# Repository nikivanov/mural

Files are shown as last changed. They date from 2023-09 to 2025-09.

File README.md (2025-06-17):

# [getmural.me](https://getmural.me)

Please find the main documentation on https://getmural.me. 

# Additional Information

## Positioning of the Drawing on the Wall

Here's how the image is prepared and drawn:

- The user defines the pin distance as part of the setup in the UI. For example 1 meter (or 1000mm). (This is d_pins in the image below.)
- The top margin is 20% of that distance, so the top of the image will be 200mm below the line between the two pins.
- Each side also has a 20% margin, so you'll get total of 60% of the horizontal distance, or 600mm.
- Now that we have the max width (600mm). The SVG is resized so its width is 600 and the height gets resized proportionally.
- Then a processing step is performed on the SVG to figure out what to actually draw, with each SVG unit being treated as millimeter.
- Finally it's converted into a simple format for Mural to draw, containing mostly its coordinate movement commands and pen up/down. This file is then uploaded to the microcontroller and executed line by line.

image_positioning

## Mural's Kinematic Model

Please find the kinematic model [here](KinematicModel.md).

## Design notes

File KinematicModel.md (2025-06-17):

# Mural Kinematic Model

The Mural bot is suspended on two belts. As it moves across the wall it rotates slightly,
in particular it tilts towards the center as it moves to the edges of the drawing region.

In order to achieve precise drawing abilities it is essential that Mural keeps track of its
position in space. In particular, it needs to be aware of its inclination angle as it
moves around.

## Basic Model

Here, we describe the kinematic model of Mural, which is used to derive its exact location 
and orientation in space. The model is implemented in ``movement.cpp``, in particular the function ``getBeltLengths``.

The bot is modeled as a rigid body in 2D and all features are assumed to be projected onto the wall plane.
In this representation it can be modeled as two lines: One connecting the pulley tangent points
and orthogonal to it the line which goes through the pen center and the bot's center of mass $m$. The 
two lines coincide in a reference point called $Q$. 
The distance of the two tangent points is calles $s$.
The bot's mass is assumed to be concentrated into a single point (its center of gravity) which is
located in distance $d_m$ from $Q$. The pen center is located in distance $d_p$ from $Q$ .

The relevant forces in this model are: $F_L$ applied by the left pulley, $F_R$ applied by the right pulley, 
and the gravitational force $F_G$ affecting the center of mass.

kinematic_model1

Assumptions:

- all mass is concentrated in a single point
- the belts masses are negligible
- the pin distance is much larger than the bot width $d_{pins} >> width_{bot}$ 

### Tangent points

In our model the belt connects to the bot in the tangent point of its pulley. Technically, this point 
is not fully stable: It rotates slightly around the pulley center as the bot tilts sideways.

In the following it is assumed that this rotation can be ignored, and the tangent point are fixed at
a $45^\circ$ belt angle.

tangent_point

The tangent point of the left pulley is located $q$ shifted to the right and $q$ shifted up relative to the pulley center. Likewise, the right tangent point is located $q$ left of the right pulley center and $q$ above the line connecting both pulley centers.

$q$ can be calculated from the pulley diameter $d_{pulley}$ as

$q=\frac{d_{pulley}}{2\cdot \sqrt2}$

So, for a typical pulley diameter of $d_{pulley}=12.69$ mm we get $q=4.4866$ mm .

The lenght of the line connecting the tangent point is given as the distance of the pulley axes minus $2*q$ .

## Solving for the Equilibrium State

With forces $F$ affecting the Mural bot they are moving it (translation) and rotating it by generating torques. 
We are looking for the static state of the bot, in which the forces as well as the torques cancel out.
We'll find this state by updating the values describing the bot's location, the forces and the torques 
in a consecutive and decoupled manner. I.e. while computing the forces we assume there's no torque, and while 
computing the torque there's no translating force. Updating these values repeatedly and in a loop
will lead to convergence of all quantities towards their true equilibrium states.

On a top level, we run the following steps in a loop until the quantities converge:
- compute belt angles $\varphi_L$ and $\varphi_R$
- compute forces on both belts
- compute torque on mural, solve for mural inclination $\gamma$

With the result: mural inclination $\gamma$, length of both belts in wall plane, and belt forces $F_L$ and $F_R$ .

In a subsequent step, these quantities are used to compute the belt lengths in 3D. Finally, a dilation correction is applied to account for non-rigidity of the belts under force.

## Forces

In the equilibrium state the overall torque on the bot is zero and can be ignored. In this case
all forces can be assumed to be applied to a single point:

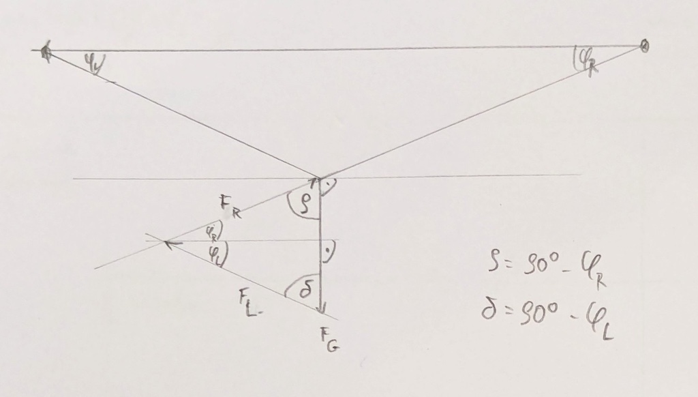
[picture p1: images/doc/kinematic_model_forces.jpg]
kinematic_model_forces


Introducing the angles $\rho = 90^\circ-\varphi_R$ and $\delta = 90^\circ-\varphi_L$ we can apply the [Law of Sines](https://en.wikipedia.org/wiki/Law_of_sines) and get:

$\frac{F_R}{F_G}=\frac{\sin(\delta)}{\sin\left( \varphi_R + \varphi_L \right)}$

$\Leftrightarrow F_R=\frac{F_G\cdot\sin(\delta)}{\sin\left( \varphi_L + \varphi_R \right)} =
\frac{F_G\cdot\cos(\varphi_L)}{\sin\left( \varphi_L + \varphi_R \right)}$

and likewise

$\frac{F_L}{F_G}=\frac{\sin(\rho)}{\sin\left( \varphi_L + \varphi_R \right)}$

$\Leftrightarrow F_L=\frac{F_G\cdot\sin(\rho)}{\sin\left( \varphi_L + \varphi_R \right)} =
\frac{F_G\cdot\cos(\varphi_R)}{\sin\left( \varphi_L + \varphi_R \right)}$

## Torques

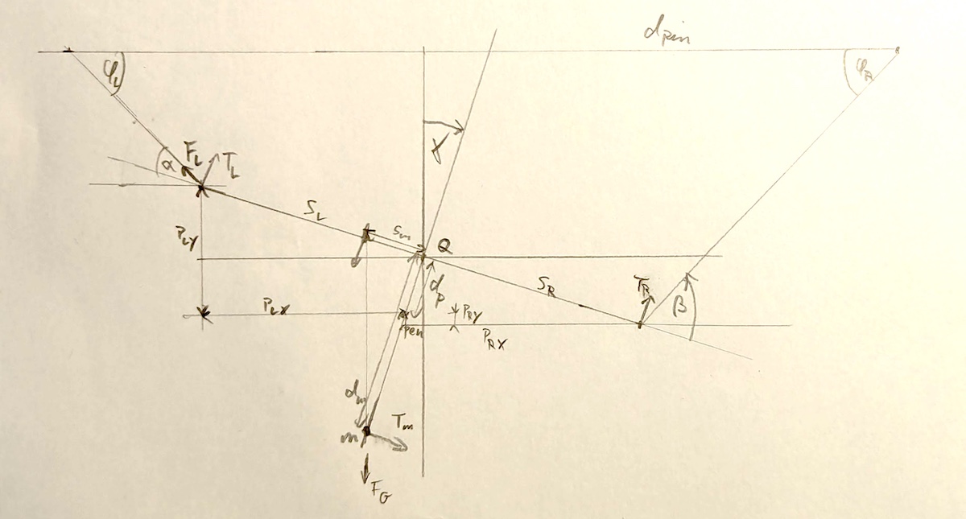
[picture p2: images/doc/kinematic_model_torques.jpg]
kinematic_model_torques


Given the forces we can compute the torque values $T_L$ ,  $T_R$ and  $T_m$ they induce around the reference point $Q$.
What we are interested in is the bot inclination angle $\gamma$. A positive $\gamma$ means the bot tilts to the right,
while a negative $\gamma$ represents a tilt to the left.

Let's introduce the auxilliary angles $\alpha$ and $\beta$ representing the direction of the belts relative to the
line connecting the tangent points:
$\varphi_L = \alpha + \gamma$
and 
$\varphi_R = \beta - \gamma$ .

As $Q$ is located in the center between the tangent points we get $s_L = 0.5\cdot s$ and $s_R = 0.5\cdot s$.

The torque induced on the left tangent point is 

$T_L = s_L \cdot \sin(\alpha)\cdot F_L$ 

, and it is pushing the bot clockwise.

Analogously, $T_R$ is affecting the right tangent point and rotating the bot counter-clockwise around $Q$:

$T_R = s_R \cdot \sin(\beta)\cdot F_R$ 

The gravity force $F_G$ of the bot results in torque $T_m$ which is rotating it counter-clockwise (for $\gamma>0$):

$T_m = s_m \cdot F_m$ , with

$s_m = d_m \cdot \tan(\gamma)$ and

$F_m = F_g \cdot \cos(\gamma)$ .

So we get

$T_m = d_m \cdot \tan(\gamma) \cdot F_G \cdot \cos(\gamma)$

In the static state the resulting torque is zero, so

$T_R - T_L + T_m \stackrel{!}{=} 0$

, and the implementation searches numerically for a $\gamma$ which fulfills this condition.

## Tangent Points given Pen Location

As our goal is to compute the precise belt lenths, we have to compute the exact tangent point location given the outcome
of the optimization operation (see ``Movement::getLeftTangentPoint``). For the left tangent point we calculate the distance from the 
pen center in $x$ and $y$ as

$P_{LX} = s_L \cdot \cos(\gamma) - d_p \cdot \sin(\gamma)$

$P_{LY} = s_L \cdot \sin(\gamma) + d_p \cdot \cos(\gamma)$

and with these the left tangent point coordinates as

$x_{PL} = x_{pen} - P_{LX}$

$y_{PL} = y_{pen} - P_{LY}$

In the same way we get for the right pulley:

$P_{RX} = s_R \cdot \cos(\gamma) + d_p \cdot \sin(\gamma)$

$P_{RY} = s_R \cdot \sin(\gamma) - d_p \cdot \cos(\gamma)$

and

$x_{PR} = x_{pen} + P_{RX}$

$y_{PR} = y_{pen} + P_{RY}$

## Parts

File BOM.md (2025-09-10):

# Bill of Materials
All parts can be found on Amazon, AliExpress, Ebay etc. Make sure the items you're ordering match the pictures. Listed prices are the lowest I could find on AliExpress.

| Part| Reference Photo | Price | Notes
|---|---|---|---|
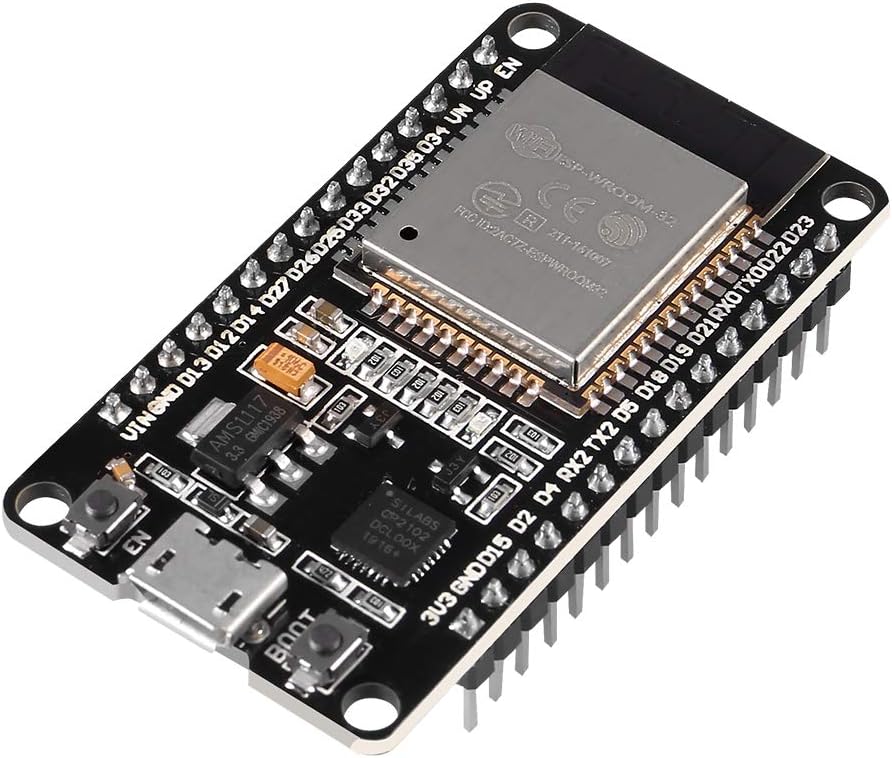
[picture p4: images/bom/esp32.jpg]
esp32
|NodeMCU ESP32 ESP-WROOM-32|| $4 | 30 pin version
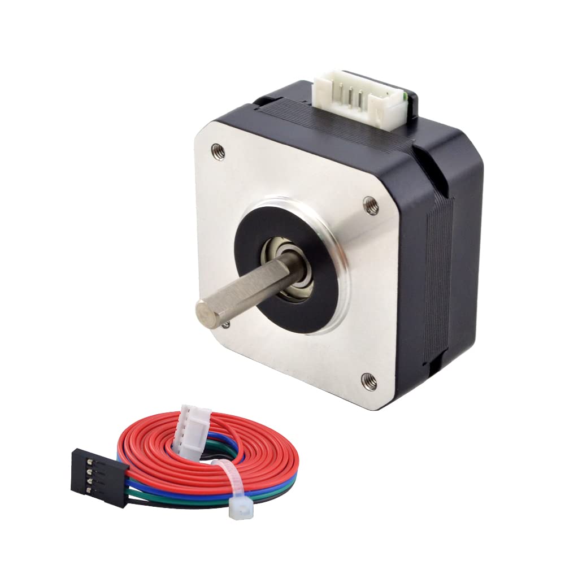
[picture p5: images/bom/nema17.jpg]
nema17
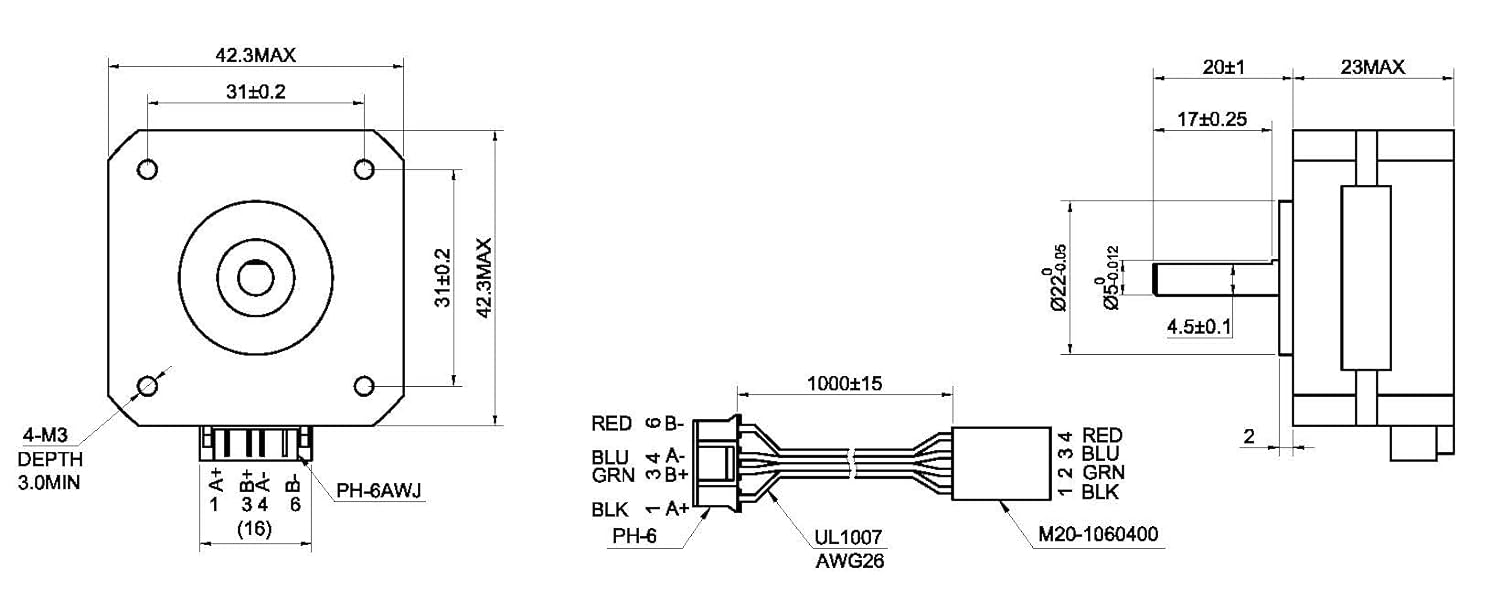
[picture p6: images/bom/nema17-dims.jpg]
nema17-dims
| 2x STEPPERONLINE Pancake Nema 17 motors |  | $18 | 
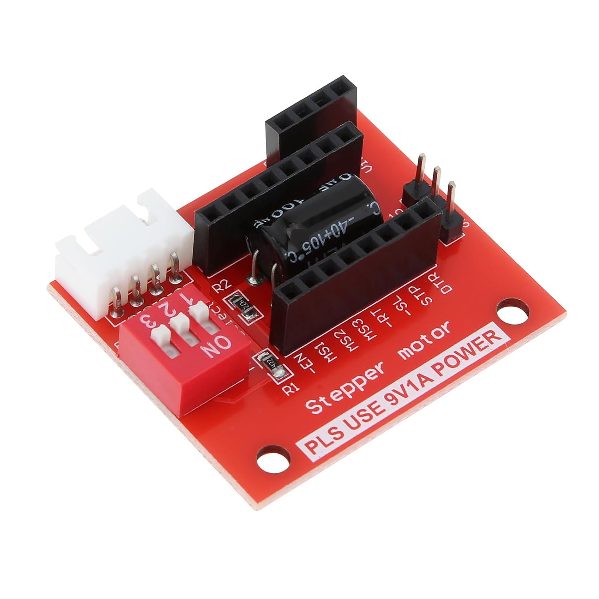
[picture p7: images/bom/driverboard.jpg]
driverboard
| 2x Stepper Motor Driver control extension boards | | $2 |
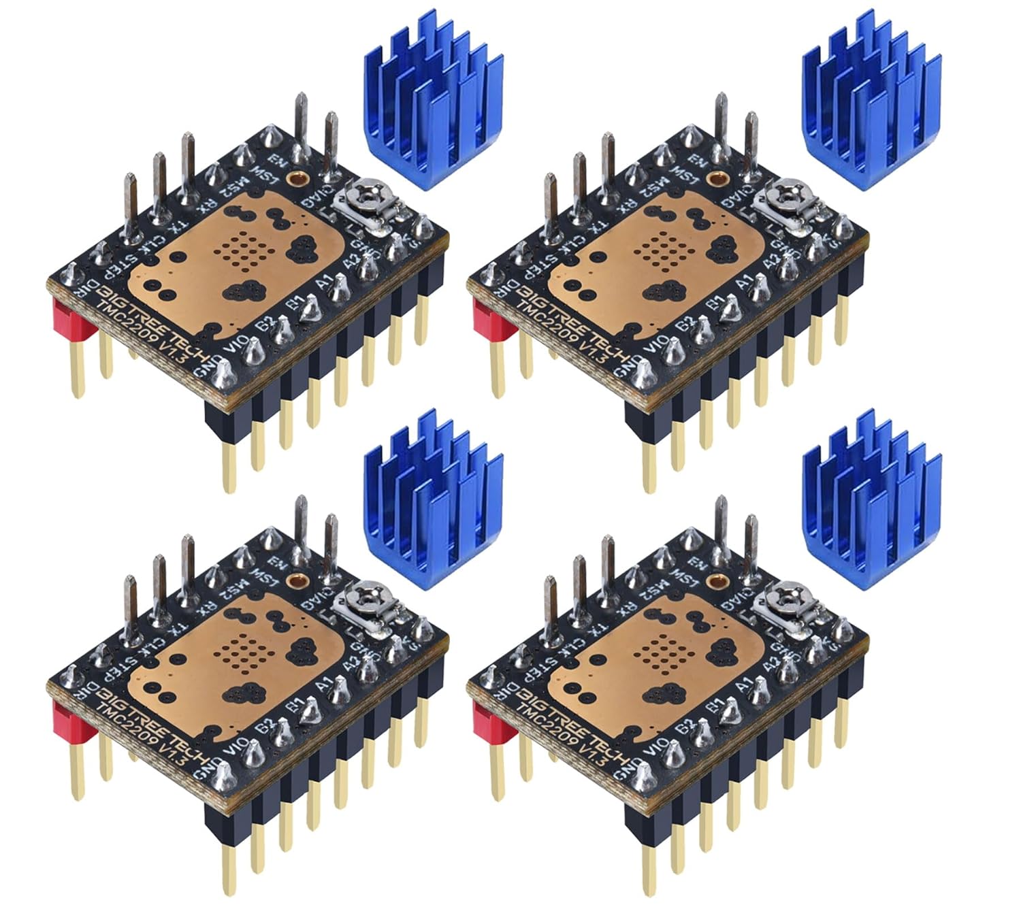
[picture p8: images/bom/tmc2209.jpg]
drivers
| 2x BigTreeTech TMC2209 Stepper motor drivers | | $14 |
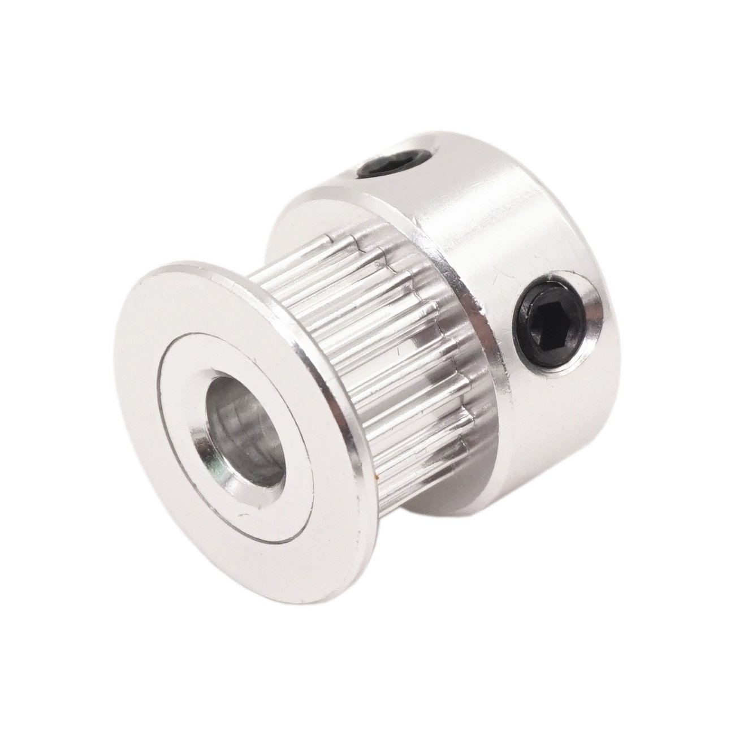
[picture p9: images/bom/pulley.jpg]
pulley
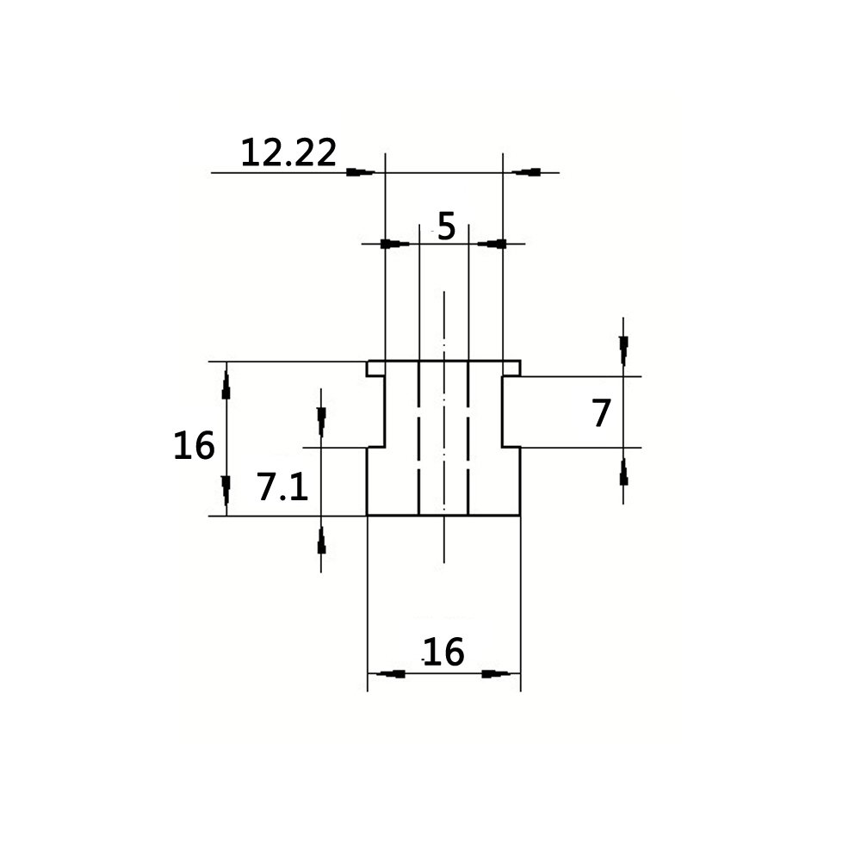
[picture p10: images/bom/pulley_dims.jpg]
pulley-dims
| 2x GT2 Pulley 20 teeth 5mm bore 6mm shaft |   | $2 | Make sure to get the pulley with those exact dimensions
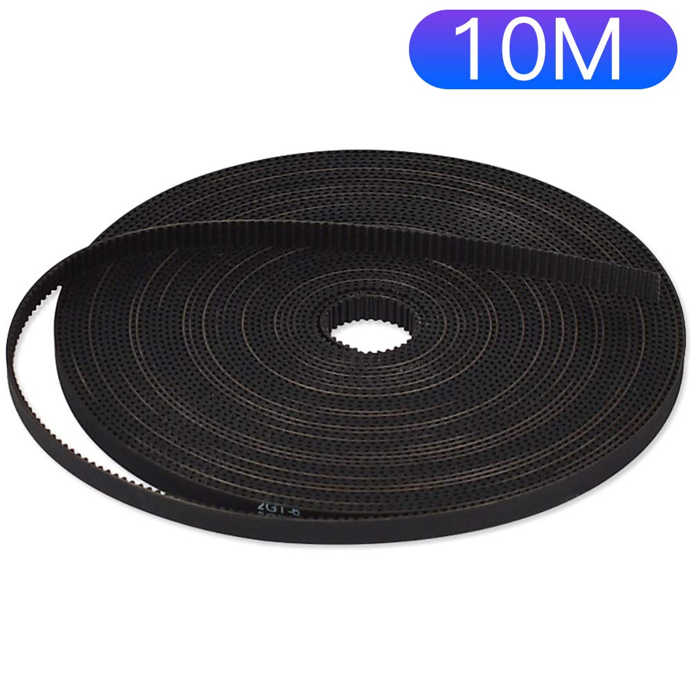
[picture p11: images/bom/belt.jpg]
belt
| GT2 Timing belt 2mm pitch 6mm width |  | $6 |
| MG90s metal gear servo | servo | $2 |
| USB-C PD trigger module | display | $1 |
| LM2596 step down voltage regulator | buck | $1 |
| 30W USB-C power delivery adapter | power | $3 | You can use any PD adapter with at least 30W and can supply 12V 
| USB-C male-to-male 10ft cable | cable | $1 |
| M-F and F-F breadboard jumper wire 10cm and 20cm | wire | $2 |
| M3 hex bolt set | m3 | $2 | You'll need 6/8/12/25 mm bolt lengths 
| 2.54m pitch male headers | headers | $1 |
| M3 heat inserts | inserts | $1 | Optional - only one is used for the pen, and you can use an M3 bolt without it
| 12mm M3 thumbscrew | thumbscrews | $1 |Optional, but sure is nicer. You only need 1 
| 10cm stepper motor cable | steppercable | $2 | These are surprisingly hard to find, I bought mine on AliExpress. You can also simply cut and solder together the long cables that came with your steppers

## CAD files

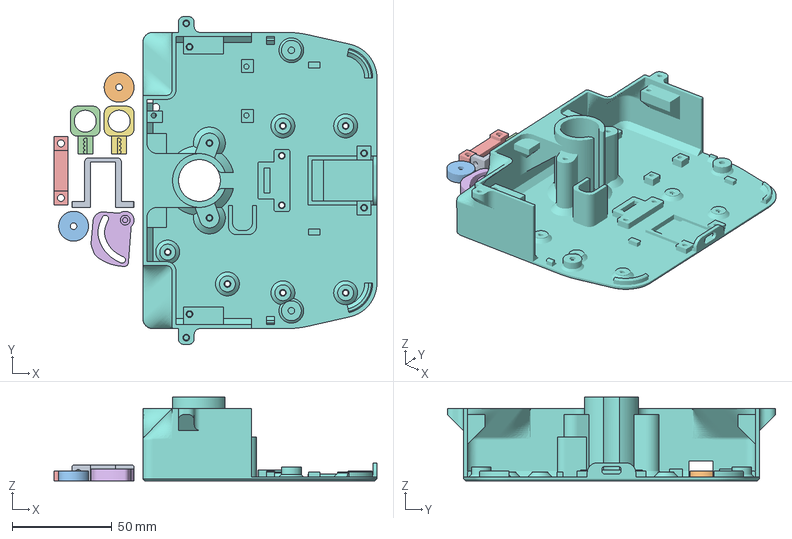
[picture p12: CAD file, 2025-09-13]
STLs/white parts.3mf
162.2 x 164.8 x 42.0 mm
white parts_1
white parts_2
white parts_3
white parts_4
white parts_5
white parts_6
white parts_7
bottom.stl

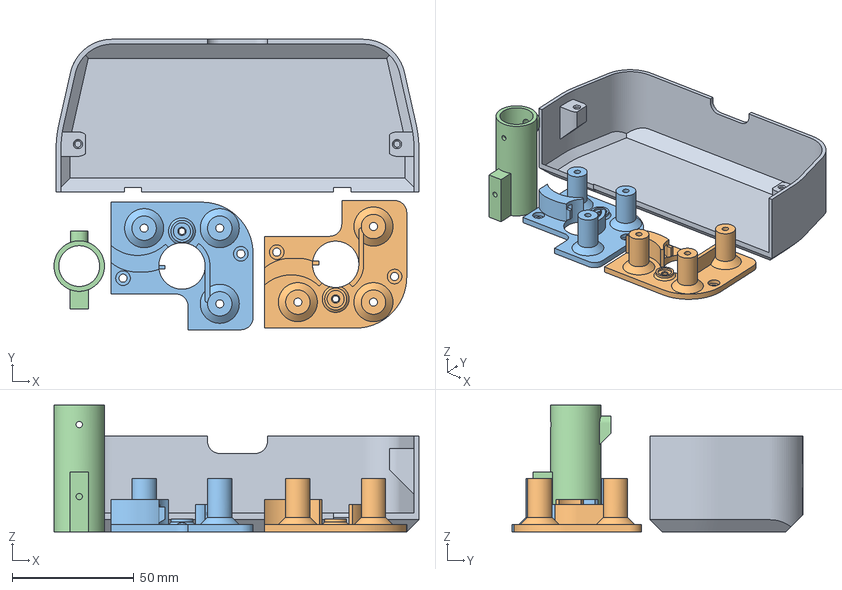
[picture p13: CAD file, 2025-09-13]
STLs/black parts.3mf
149.6 x 119.1 x 52.0 mm
black parts_1
left motor carrier.stl
right motor carrier.stl
black parts_4

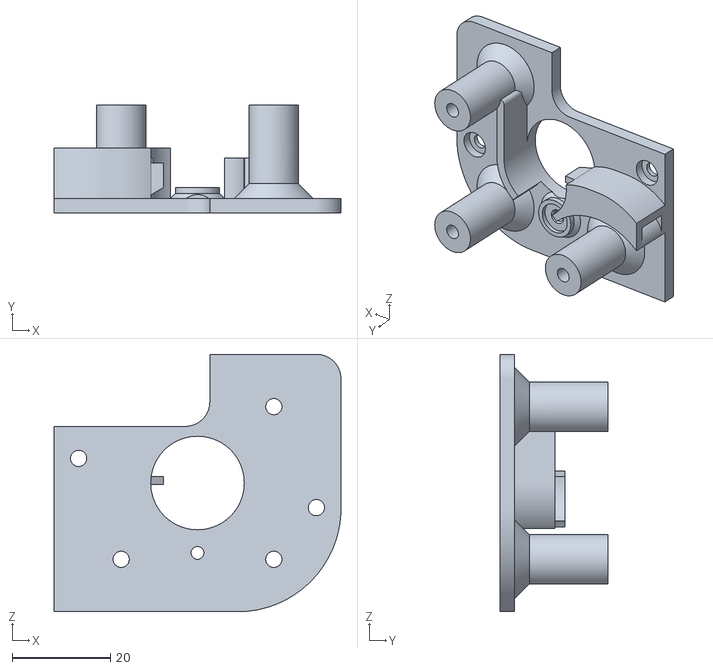
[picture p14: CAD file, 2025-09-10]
STLs/right motor carrier.stl
58.3 x 22.0 x 52.3

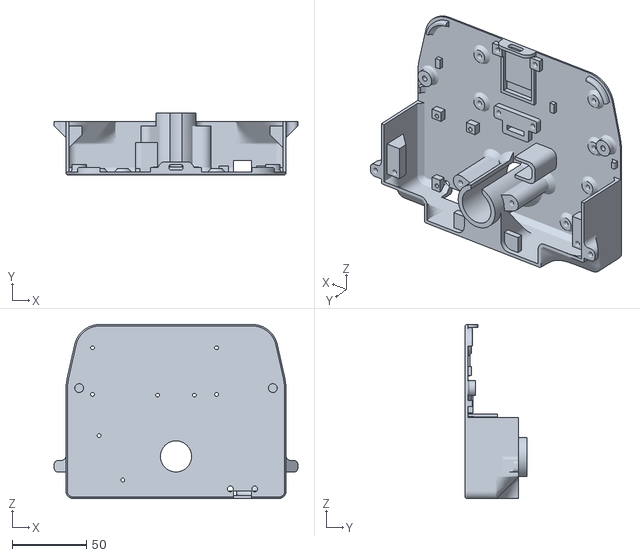
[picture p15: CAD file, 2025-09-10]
STLs/bottom.stl
164.8 x 42.0 x 117.6

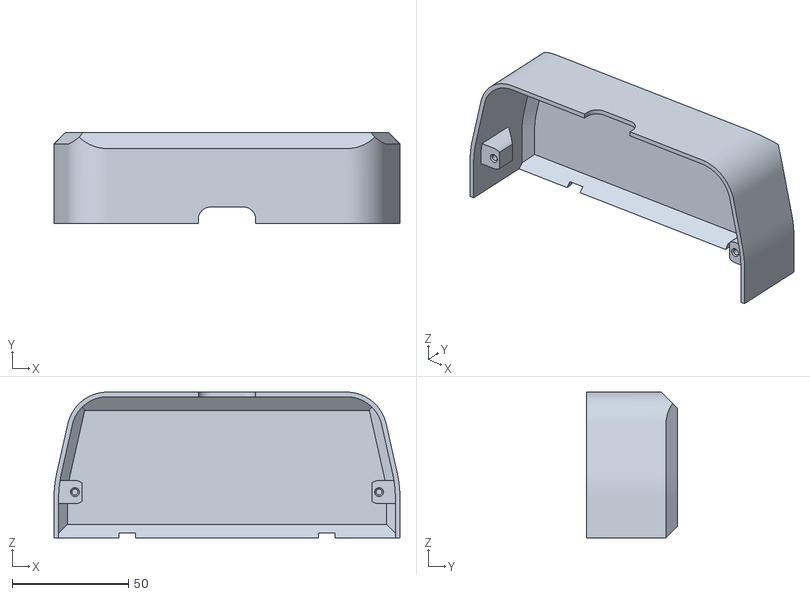
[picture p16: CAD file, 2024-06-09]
STLs/cover.stl
148.8 x 39.3 x 62.7

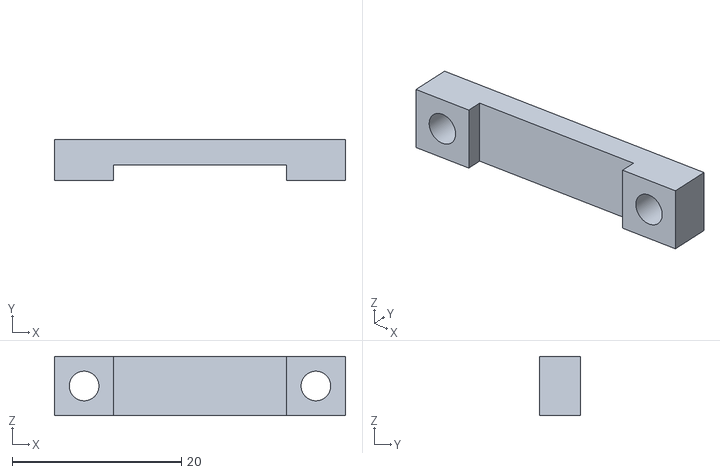
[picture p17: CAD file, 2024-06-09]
STLs/PD clamp.stl
34.4 x 4.85 x 7.00

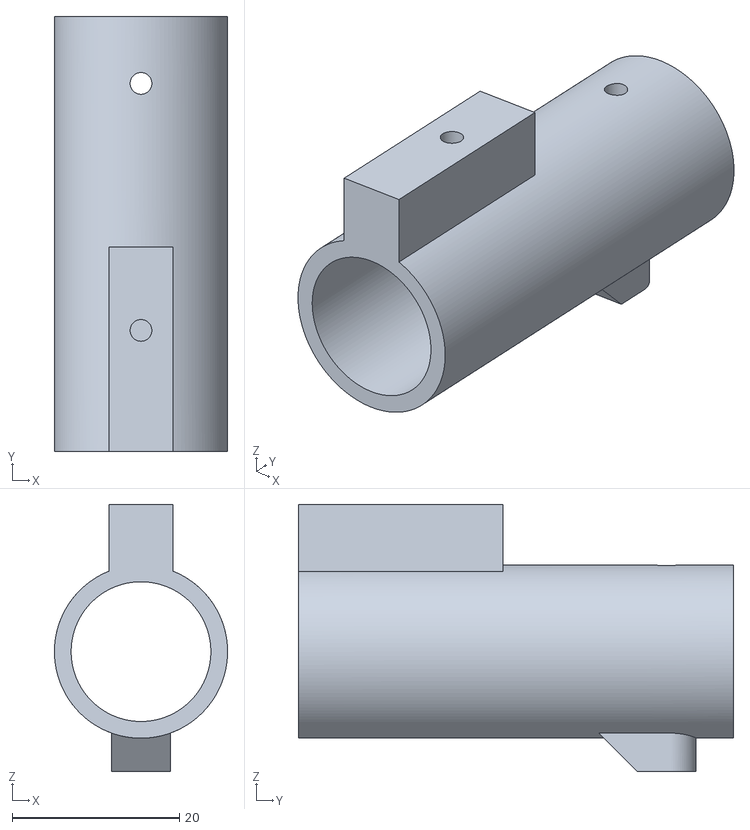
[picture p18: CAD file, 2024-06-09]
STLs/pen.stl
20.7 x 52.0 x 32.0

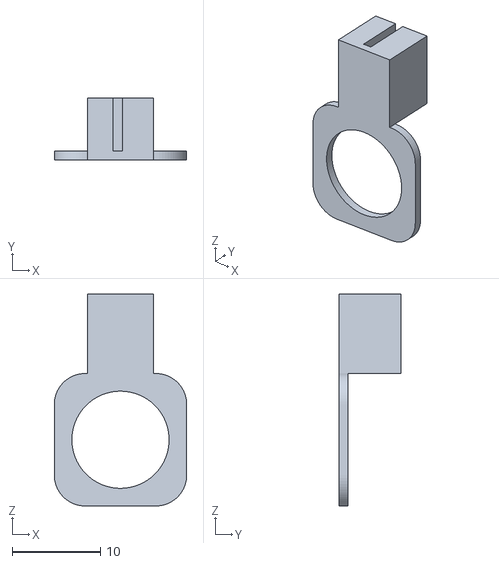
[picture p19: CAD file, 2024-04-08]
STLs/left belt loop.stl
15.0 x 7.00 x 24.0

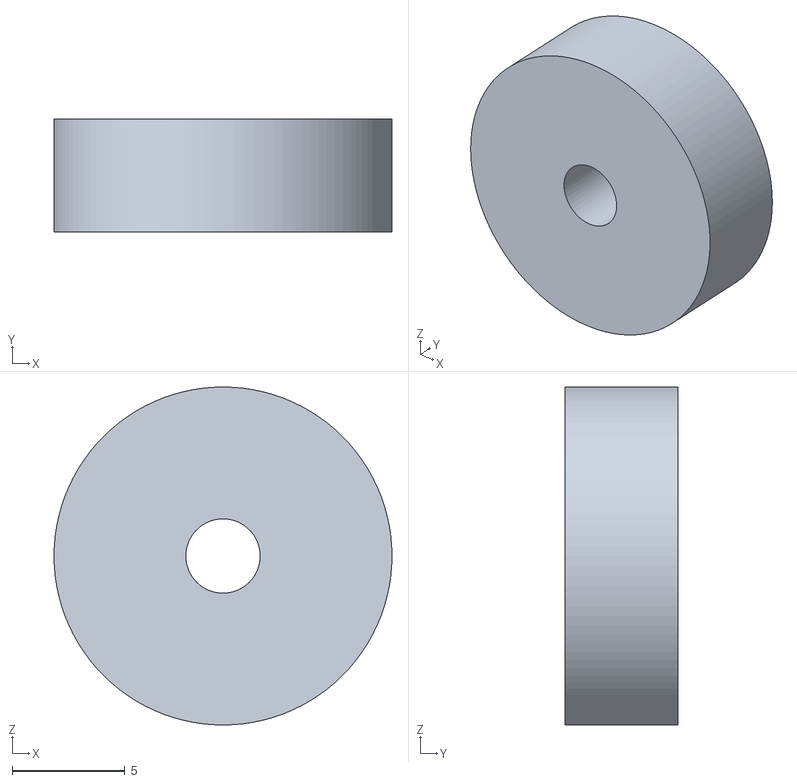
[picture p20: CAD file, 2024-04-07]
STLs/idler.stl
15.0 x 5.00 x 15.0

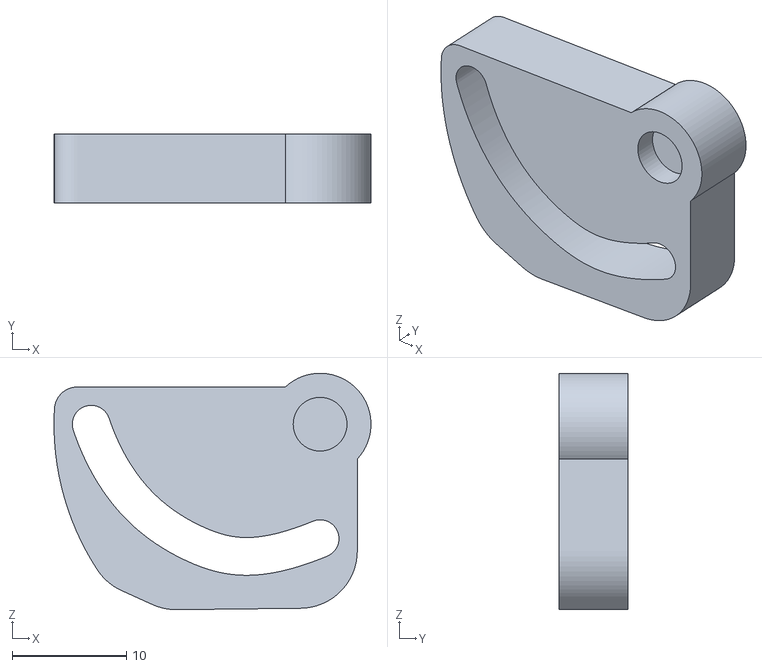
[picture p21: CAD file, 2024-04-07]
STLs/servo pen driver.stl
27.7 x 6.00 x 20.6

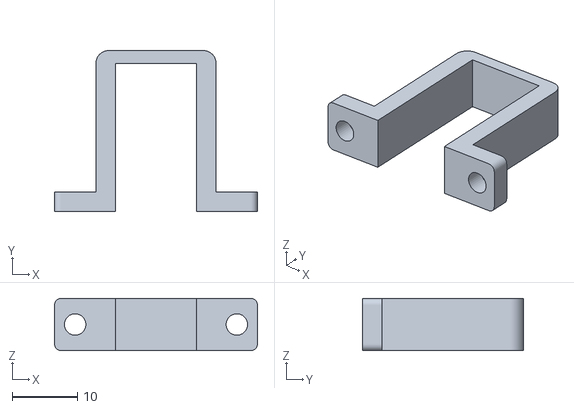
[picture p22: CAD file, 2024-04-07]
STLs/servo clamp.stl
31.2 x 24.8 x 8.00

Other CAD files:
STLs/left motor carrier.stl
STLs/right belt loop.stl

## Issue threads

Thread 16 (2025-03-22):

GCODE

rwlloyd, 2025-03-22:
Hi. Just watched your video and thought. 'Damn, this guy has done all the things I couldn't be bothered to do when I made a wall plotter a few years ago'. I approached from the modded 3D printer direction though.. RAMPS board, [Marlin-polargraph](https://github.com/i-make-robots/Marlin-polargraph) and motors suckered to a window. It was a mess of wire and a pain to set up. Your solution is much neater. Well done!

What might work is to marry the frontend and hardware that you've designed and have another board interpret gcode. The mural board would feed the gcode over serial to the GRBL board (any arduino based or the atmega328). Then 'mural-GRBL' (preconfigured for delta kinematics) handles all of the motor control.

I think that leveraging and modifying what you already have running and then having mural firmware interpret gcode would be my ideal plotter and I'd start drawing on the big windows at work asap. Your system looks very much simpler and neater than my efforts.

I guess this is not strictly an issue but I'm going to print a mural when I get the chance. Just for the hardware design I will thank you in advance.

nikivanov, 2025-03-25:
There is already an ESP32 compatible version of Grbl and a newer version, called FluidNC. I'm planning on adapting Mural to work with FluidNC so I can get all the movement goodies that it comes with.

Yash-xoxo, 2025-03-29:
thanks it might me a good upgrade

Closed 2025-04-01.

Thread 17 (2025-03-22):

CAD files

ModestoHagney, 2025-03-22:
Would you be willing to share the CAD files?

I'd like to build one of these with some parts I have on hand but I've never had much luck imorting STLs into fusion.

nikivanov, 2025-03-25:
Yep, I keep forgetting to upload F3D and STEP files. I will do it in the next few days. I'll ping this thread when it's done.

nikivanov, 2025-03-26:
https://github.com/nikivanov/mural/blob/main/STLs/Mural.step here it is!

Closed 2025-03-27.

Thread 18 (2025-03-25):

Build notes/park servo error

PangeaPrint, 2025-03-25:
First off great work! Couple things:

1. The "Park Servo" button doesn't do anything for me to control the pen holder servo. When plugged in it goes to the in/up position on boot up which works but when attaching the linear motion piece it needs to be put on in a different orientation than the video. It's really not an issue with functionality yet just wanted to add that note if anyone is seeing the same. Properly orienting it allows it to work when adjusting distance later in the prep menu.

2. Here's the wiring for the L/R servos:

4pin side               6 pin side
1-2-3-4---------------4-EMPTY-1-3-EMPTY-2
ex. Black-Green-Blue-Red------------------Red-EMPTY-Black-Blue-EMPTY-Green

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

I have the entire unit built/wired/wifi connected but one of the L/R stepper control boards showed up with the voltage adjustment screws busted so it's stuck at low voltage and won't operate under a load (ie it's own weight) without skipping until the new one comes tomorrow. That being said everything is acting correctly during bench testing.

I'm using a generic ESP32 (ESP-WROOM-32 ESP32 ESP-32S Development Board from Amazon) since I had it floating around so that may cause issue as well. I'll update tomorrow if I can get it to draw.

nikivanov, 2025-03-26:
You're absolutely right! When I was reshuffling the screens I forgot to add servo control to the Set Top Distance screen. I'll fix it now.

nikivanov, 2025-03-26:
@PangeaPrint I just uploaded the new firmware - could you try reflashing your ESP32 and let me know if that fixes your servo issue?

PangeaPrint, 2025-03-26:
Yup, that worked! One more question, not sure what the Extend 100mm (e-steps calibration) button is for but I don't see it making any movements.

nikivanov, 2025-03-26:
Yeah that one is broken too - I haven't used it in ages. I wrote it to verify the extrusion length during initial design. I'll fix it at some point.

Closed 2025-03-29.

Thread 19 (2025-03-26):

Heat inserts?

canadaohcanada, 2025-03-26:
I didn’t see the heat inserts being used in the assembly video. Is there a specific place they need to be used or is it more of a “nice to have”?

nikivanov, 2025-03-26:
7:30 into the assembly video

canadaohcanada, 2025-03-26:
Brilliant. I was watching with the sound off. Thank you for the accurate timestamp.

Closed 2025-03-26.

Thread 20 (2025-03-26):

Upload to Mural failed! [object Object] error

PangeaPrint, 2025-03-26:
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

Hitting "OK" then reloading the page is the work around.

Chrome
OSX

nikivanov, 2025-03-27:
Hmm, never seen this before. First thing we gotta do is get the actual error. I'm going to fix that e-steps calibration bug that you found and also add some code that will print the actual error instead of just the object

nikivanov, 2025-03-27:
@PangeaPrint try now please - it should be fixed. ESteps calibration should also be fixed.

Closed 2025-03-29.

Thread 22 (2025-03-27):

3d Files for byj48 Version (as seen in your Video) with unipolar to bipolar mod and MKS-DLC32

flow1986, 2025-03-27:
Hi,
very nice Project! would it be possible for you to upload the BYJ48 Stepper Version Stls?

You can use these motors with an Bipolar mod and some Bipolar Motor Drivers for more torque and less lost steps.

i want to rebuild your Mural Walldrawer with an mks-dlc32 (https://github.com/makerbase-mks/MKS-DLC32)

because it would be even cheaper and with the mks-dlc32 everything is on board (esp32, stepper driver, power supply)

i have all parts at home, because i wanted to build a wallplotter with FluidNC, but didn´t have the time yet...

thanks Flo

nikivanov, 2025-03-27:
Sure, but I wont be able to provide any support for it, and the existing firmware won't work on it. If that sounds good I can upload the STEP file

flow1986, 2025-03-27:
That Sounds perfect for me!
Thank you

Nik Ivanov ***@***.***> schrieb am Do., 27. März 2025, 15:44:

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

nikivanov, 2025-03-27:
https://github.com/nikivanov/mural/blob/28byj-48/STLs/prototype%20v8.step

Closed 2025-03-27.

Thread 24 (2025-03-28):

a problem with online firmware burning

APT-H, 2025-03-28:
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

I loved your project and planned to build one at home and play with my kids, but now the program is having a problem.

As the screenshot, I use the development board is ESP32-D0WD-V3, successfully connected to the computer, but after the motor burning, it is stuck in this step, but also waiting for a lot of time, always the same. I've replaced three computers and they all seem to have the same problem. At first, I thought that the development board was broken, but when I burned projects online in other places, I was able to burn normally and successfully run the firmware of other projects. It's weird. It's bothering me

APT-H, 2025-03-29:
I burned the source code using VSCode and it was successful.

Closed 2025-03-29.

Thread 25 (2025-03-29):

Change pins in software

ModestoHagney, 2025-03-29:
Would it be possible to add the ability to change the pins, and maybe some other settings like speed and servo positions in software?

The setpper board I'm working with uses pinouts that are different to the ones in the code.
I did manage to recompile and change the pins but I had heaps of issues getting it to compile.

nikivanov, 2025-03-29:
Hi! I'm not going to be adding support for other boards to Mural, since its hardware and software are interdependent. You're welcome to fork the repo and add these abilities if you want to make the software more generic. It sounds like you got the firmware to recompile, so you're already half way there.

ModestoHagney, 2025-03-30:
Fair enough. I had a hell of a time getting it to compile, something to do with WifiManager.git but I managed to get it on there in the end.

Closed 2025-03-30.

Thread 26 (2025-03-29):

Coordinate conversion code

CIRCUIT-RAPTOR, 2025-03-29:
Hi. I'm trying to implement a similar plotter using Raspberry pi Zeo 2W. I would like to know how the svg file uploaded is converted to coordinates for the stepper motor. Is there a specific code for doing this operation? I just want to know how the svg is converted to the final form as seen in the drawings.

nikivanov, 2025-03-29:
The code runs in your browser, with some of it running in the web worker. I rasterize and re-vectorize SVGs to account for this like stroke width.

Here's the vectorization call to the web worker: https://github.com/nikivanov/mural/blob/4682db1fa4d548cf25d1176ae29ae6e4425b6ff8/data/www/main.js#L167

Here's the call to the web worker that converts the re-vectorized SVG into a list of commands for Mural: https://github.com/nikivanov/mural/blob/4682db1fa4d548cf25d1176ae29ae6e4425b6ff8/data/www/main.js#L206

Web worker code is written in typescript and then webpacked. Here's the entry point of rendering the SVG into a list of commands: https://github.com/nikivanov/mural/blob/4682db1fa4d548cf25d1176ae29ae6e4425b6ff8/tsc/src/main.ts#L39

CIRCUIT-RAPTOR, 2025-04-03:
I was able to replicate the outline drawing function. But I'm not able to achieve the infill/crosshatch pattern in those dark areas. Any advice on how to make this work? Also, I might switch to an ESP-32 if this turns out to be unsuccessful, because I need this to be completed within 2 weeks. I'm trying to use things available at my house, that is why I went for the pi, 28byj-48 stepper motors and ULN2003 driver. If I had to use the ESP-32, would the program flashed in it via the mural website be able to run these 28byj-48 stepper motors? I saw them on your video that it was used in the first iteration.
Thanks

nikivanov, 2025-04-03:
The SVG processor will shade in any paths that have a non-white non-transparent infill. The density of the crosshatch infill is governed by this property: https://github.com/nikivanov/mural/blob/4682db1fa4d548cf25d1176ae29ae6e4425b6ff8/tsc/src/main.ts#L97

You won't be able to use the current firmware with 28byj-48 - they are driven completely differently from the steppers that I'm using.

CIRCUIT-RAPTOR, 2025-04-05:
I'm still not able to successfully create an infill code. So, I'm now using an esp-32 to flash the firmware through mural website. But I'm getting stuck at erasing flash. I've read a solved issue about the same and saw that he flashed it via VS Code in the end. Is there any fix?

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

nikivanov, 2025-04-05:
Try some of the suggestions in this thread and let me know if it helps: https://github.com/nikivanov/mural/issues/30

CIRCUIT-RAPTOR, 2025-04-05:
I've also tried those. I don't think my problem is with connecting, as from the picture it is clear that the device is connected and is able to recognize it. I tried to flash it via VS Code with Platform IO. But I'm getting errors while building:

Processing esp32dev (platform: espressif32; board: esp32dev; framework: arduino)
---------------------------------------------------------------------------------------------------------------------------------------------------------
Verbose mode can be enabled via `-v, --verbose` option
CONFIGURATION: https://docs.platformio.org/page/boards/espressif32/esp32dev.html
PLATFORM: Espressif 32 (6.10.0) > Espressif ESP32 Dev Module
HARDWARE: ESP32 240MHz, 320KB RAM, 4MB Flash
DEBUG: Current (cmsis-dap) External (cmsis-dap, esp-bridge, esp-prog, iot-bus-jtag, jlink, minimodule, olimex-arm-usb-ocd, olimex-arm-usb-ocd-h, olimex-arm-usb-tiny-h, olimex-jtag-tiny, tumpa)
PACKAGES:
 - framework-arduinoespressif32 @ 3.20017.241212+sha.dcc1105b
 - tool-esptoolpy @ 1.40501.0 (4.5.1)
 - toolchain-xtensa-esp32 @ 8.4.0+2021r2-patch5
LDF: Library Dependency Finder -> https://bit.ly/configure-pio-ldf
LDF Modes: Finder ~ chain, Compatibility ~ soft
Found 42 compatible libraries
Scanning dependencies...
Dependency Graph
|-- WiFiManager @ 2.0.17+sha.32655b7
|-- ESPAsyncWebServer @ 3.7.4+sha.25845e7
|-- ESP32Servo @ 3.0.6+sha.e697ea7
|-- Adafruit SSD1306 @ 2.5.13+sha.78d6a13
|-- AccelStepper @ 1.64.0
|-- ArduinoJson @ 5.13.4
|-- SPIFFS @ 2.0.0
|-- AsyncTCP @ 3.3.8
|-- ESPmDNS @ 2.0.0
|-- FS @ 2.0.0
|-- Wire @ 2.0.0
Building in release mode
Transpiling TS code
rm data/www/worker/* || true
'rm' is not recognized as an internal or external command,
operable program or batch file.
'true' is not recognized as an internal or external command,
operable program or batch file.
*** Error 1
npm run build
'npm' is not recognized as an internal or external command,
operable program or batch file.
*** Error 1
cp dist_packed/main.js ../data/www/worker/worker.js
'cp' is not recognized as an internal or external command,
operable program or batch file.
*** Error 1
Retrieving maximum program size .pio\build\esp32dev\firmware.elf
Checking size .pio\build\esp32dev\firmware.elf
Advanced Memory Usage is available via "PlatformIO Home > Project Inspect"
RAM:   [==        ]  15.2% (used 49796 bytes from 327680 bytes)
Flash: [========  ]  81.6% (used 1069577 bytes from 1310720 bytes)
============================================================== [SUCCESS] Took 8.94 seconds ==============================================================

I tried uploading. Even though it shows successful upload, I am not able to find the esp hotspot. I tried monitoring it and it shows a SPIFFS mounting error.

I'll provide an update if I find a fix.

nikivanov, 2025-04-05:
What OS are you running? rm and cp are Linux terminal commands.

I'll provide a script you can run to flash the firmware locally.

On Sat, Apr 5, 2025, 10:51 AM CIRCUIT-RAPTOR ***@***.***>
wrote:

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

CIRCUIT-RAPTOR, 2025-04-05:
I'm on windows 11.

nikivanov, 2025-04-05:
I'd recommend you use wsl to compile the firmware yourself. I'll also
provide a python script to flash the firmware locally

On Sat, Apr 5, 2025, 11:21 AM CIRCUIT-RAPTOR ***@***.***>
wrote:

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

nikivanov, 2025-04-06:
@CIRCUIT-RAPTOR I wonder if you have the same error in your browser console as here: https://github.com/nikivanov/mural/issues/30#issuecomment-2781172557

CIRCUIT-RAPTOR, 2025-04-08:
Thank you. Finally flashed it via the website you provided.
https://getmural.me/firmware_flasher_slow.html

Closed 2025-04-08.

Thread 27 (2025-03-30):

CDN 404 Error on https://cdn.jsdelivr.net/npm/less.min.js.map

jp3141, 2025-03-30:
https://cdn.jsdelivr.net/npm/less.min.js.map returns 404, Failed to resolve the requested file.

Therefore the mural web page doesn't show the gear icon or provide any way to access the settings.

Closed 2025-03-30.

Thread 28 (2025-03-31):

GT2 drive belt slipping

litxaohu, 2025-03-31:
Thanks to the author for open sourcing the project, I have successfully reproduced it.

However, the buckle 3D file with the belt fixed does not seem to be suitable. It is difficult to fix and causes the belt to fall off. I tried the 4mm and 2mm 3D printer extrusion heads, but the results are similar.

I designed a new fixed clap, which uses the friction between the belts to fix, and the precision requirement of the printer is relatively low. I hope the author can answer my related question. There are some differences between the size of the clasp and the original one, will it affect the printing accuracy?

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

Thanks again to the author for the project, it's a great design.
I have attached all my [printed documents here](https://github.com/litxaohu/mural/blob/main/GT2_v2.stl).

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

nikivanov, 2025-03-31:
Do you mean that the belt does not stay in the hanger and falls out? If so, you can try the trick I suggest in the video - cut the end of the belt so it has a frayed end and that little extra material would make it sit better in the hanger belt trough.

If you're using your own hangers, the accuracy should not be affected as long as you home the device by placing the hanger loops on the homing bolts.

litxaohu, 2025-04-01:
I checked your video carefully and I found that the belt I bought may be a little different, when I cut off the end of the belt, it will not become rough and therefore difficult to secure.

nikivanov, 2025-04-01:
I see. Your hanger should work just fine then. Worst case you can just hot glue the belts into the hangers.

Closed 2025-04-03.

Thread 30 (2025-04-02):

Firmware Flasher

toxict0ast, 2025-04-02:
Very cool project! I'm excited to try it. Sadly, amazon sent the wrong pully, so I'm waiting on that.

I can't seem to get the webflasher to work.

1. I installed the CP210x_Windows_Drivers
2. Held down boot, pluged in the USB, let go of boot button.
3. Clicked "Flash firmware" and I just get stuck here

esptool.js
Serial port WebSerial VendorID 0x10c4 ProductID 0xea60
Connecting...

Detecting chip type...ESP32
Chip is ESP32-D0WD-V3 (revision 3)
Features: Wi-Fi, BT, Dual Core, 240MHz, VRef calibration in efuse, Coding Scheme None
Crystal is 40MHz
MAC: d8:13:2a:2f:4a:08
Uploading stub...
Running stub...
Stub running...
Changing baudrate to 460800
Changed
Erasing flash (this may take a while)...

I have tried a few USB cord, edge/chrome, and 2 different ESP32 boards. I am able to flash other things to it, like ESPhome as a test. Any ideas what am I doing wrong?

nikivanov, 2025-04-02:
I've never seen it crash there. No idea, sorry. Please let me know if you figure it out. Try checking chrome devtools console log for errors.

nikivanov, 2025-04-02:
Comparing the output you posted above to the one I get from my board, your board's chip is ESP32-D0WD-V3 (revision 3) and mine is ESP32-D0WDQ6 (revision 1). Unless you're on a super tight budget, I suggest buying the ESP32 from the Amazon link from the BOM and seeing if that resolves your issue.

Also, another person was telling me about their problems with flashing their controller and they found a somewhat surprising solution - try it first before buying another set of boards?

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

twofieros, 2025-04-02:
I had similar issues with Chrome on my Mac when trying to flash. To get it to work I held down both buttons when plugging in. Release them one at a time with about 5 seconds between plugging in and releasing. Release the boot button last.

toxict0ast, 2025-04-02:
@nikivanov  Thanks for replying! I will try you and @twofieros  suggestions.

I did buy the one you linked on amazon. But I wouldn't be surprised if amazon made a mistake. The also sent me the wrong pulleys.

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

nikivanov, 2025-04-02:
This definitely looks like the correct board, just a newer revision of mine. Let me know any of the suggestions above make it work for you!

grantmatson, 2025-04-06:
I'm running into the same issue.  My board is the same ESP32-D0WD-V3 (revision 3), which was purchased directly from the BOM.  I've tried all the suggestions in this thread and it still freezes on the "Erasing Flash (this may take a while)...".

The console has this error:
```
bundle.js:2  Uncaught (in promise) Error: Invalid head of packet (0x78): Possible serial noise or corruption.
    at de.read (bundle.js:2:50152)
    at async Pe.readPacket (bundle.js:2:58998)
    at async Pe.checkCommand (bundle.js:2:64609)
    at async Pe.eraseFlash (bundle.js:2:70652)
    at async Pe.writeFlash (bundle.js:2:75155)
    at async HTMLButtonElement.<anonymous> (firmware_flasher.html:438:13)
```

nikivanov, 2025-04-06:
Thanks for the stacktrace! The more immediate plan is to provide a python script that flashes the firmware, but hopefully I can figure out why it works for some but not the others.

nikivanov, 2025-04-06:
A quick google search suggests two things:

-  Per https://github.com/espressif/arduino-esp32/issues/1253#issuecomment-435420119 try holding the BOOT button throughout the whole process
-  Per https://github.com/espressif/arduino-esp32/issues/1253#issuecomment-487285571 I could try to turn down the baudrate to 115200 here: https://github.com/espressif/arduino-esp32/issues/1253#issuecomment-487285571 . If you know how to do it in DevTools, try changing this value in your browser and then go through the flashing process

grantmatson, 2025-04-06:
I switched to my Macbook and it ran without any issues. I'm probably going to make a second Mural since I have all the parts for it. I'll try your suggestions on my deckstop (Windows 11), which was the system having the error.

CIRCUIT-RAPTOR, 2025-04-06:
I was able to successfully flash using WSL. But when I monitor it, I keep getting this block of output repeatedly:

rst:0xc (SW_CPU_RESET),boot:0x13 (SPI_FAST_FLASH_BOOT)
configsip: 0, SPIWP:0xee
clk_drv:0x00,q_drv:0x00,d_drv:0x00,cs0_drv:0x00,hd_drv:0x00,wp_drv:0x00
mode:DIO, clock div:2
load:0x3fff0030,len:1184
load:0x40078000,len:13232
load:0x40080400,len:3028
entry 0x400805e4
ets Jul 29 2019 12:21:46

I tried flashing a blink program using Arduino IDE and it worked well. Then I used an online ESP flashing tool. In this tool I was able to successfully erase and flash programs (an example program that lets you connect to Wi-Fi), and it had no trouble running those. But whenever I open the terminal after erasing the flash I get this error repeatedly which is similar to the one before.

[11:06:52]rst:0x10 (RTCWDT_RTC_RESET),boot:0x13 (SPI_FAST_FLASH_BOOT)
[11:06:52]invalid header: 0xffffffff
[11:06:52]invalid header: 0xffffffff
[11:06:52]invalid header: 0xffffffff
[11:06:52]invalid header: 0xffffffff
[11:06:52]invalid header: 0xffffffff
[11:06:52]invalid header: 0xffffffff
[11:06:52]invalid header: 0xffffffff
[11:06:52]invalid header: 0xffffffff
[11:06:52]ets Jul 29 2019 12:21:46

nikivanov, 2025-04-06:
@grantmatson did you install the driver on win11?

piousgreek, 2025-04-07:
Greetings, i am having similar issue to others.  i purchased the esp32 from the BOM and it identifies as ESP32-D0WD-V3.  CP210x driver is installed. however the mural web flasher is not working.  The cp210x chip on the board appears to be a knock off but i can successfully flash generic sketches from both Arduino and platformio,

when i try to build the build the project using platformio, i receive some errors and although it produces a firmware that i can flash, the esp ends up in a bootloop complaining about a missing spiff.

can you release or provide a .bin file so i can flash via esptool or some other program.

nikivanov, 2025-04-08:
Hey everyone!

If you're having trouble flashing the firmware for your controller, first try using this page instead:
https://getmural.me/firmware_flasher_slow.html

It's the same page as the original flasher but the baud rate is turned down to 115200.

If that still doesn't work for you, download this ZIP file and run the command in the readme.txt https://getmural.me/firmware/firmware.zip

Please let me know what works and what doesnt!

piousgreek, 2025-04-08:
the slower baud rate with the web flasher seems to have done the trick for me, thank you.  "Firmware flashed successfully!"

CIRCUIT-RAPTOR, 2025-04-08:
Mine also worked after flashing from https://getmural.me/firmware_flasher_slow.html
I think the problem is with the knockoff chip inside the ESP since I think mine is also a knockoff. Maybe this should be added as an alternative flashed in the mural website.
Thank you for all the effort.

nikivanov, 2025-04-08:
Excellent! I'm pushing the change to the main firmware_flasher.html now, and deleting _slow.html

Closed 2025-04-11.

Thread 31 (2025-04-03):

Connect Enable Pins on Stepper motor extension board

bkonings, 2025-04-03:
My Motors were not working somehow.

After measuring everything 10 times, verifying my connections and zooming in a lot in YouTube to make sure (does he connect the enable pins or not?) I dove into the code and found you do assign the enable pins in the code.

After I connect those everything is working as expected.

const auto LEFT_STEP_PIN = 13;
const auto LEFT_DIR_PIN = 12;
const auto LEFT_ENABLE_PIN = 14;

const auto RIGHT_STEP_PIN = 27;
const auto RIGHT_DIR_PIN = 26;
const auto RIGHT_ENABLE_PIN = 25;

So now I wondering if you just forgot to connect them up in the YouTube video?
I do use a different ESP32 board, but I don't think that explains the issue.

Thanks for the project, very interesting.

nikivanov, 2025-04-03:
That's really strange, since the motors should be enabled as their default state, so if the enabled pin is not connected they are never NOT enabled. I did make the plumbing in software for the enabled pins, but I never ended up needing a use case when the motor are not enabled. Are you using TMC2209 drivers? Per spec:
```
ENN 2 DI Enable not input. The power stage becomes switched off (all motor
outputs floating) when this pin becomes driven to a high level.
```
which should mean that motors are enabled by default as long as that pin is pulled low.

bkonings, 2025-04-04:
I agree it should work but definitely doesn't without connecting the enable pin.

I am using these: BIGTREETECH TMC2209 V1.3

(https://nl.aliexpress.com/item/33028050145.html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)

ESP32 I am using: ESP32 Dev Kit C V4

As I can connect the enable pin it is fine, just wanted to share my experience ;)

nikivanov, 2025-04-04:
Yep, I appreciate you providing the workaround! Looking at AliExpress link, those are version 1.2 whereas Amazon's are 1.3. Unlikely that it's the culprit, but maybe 1.2 doesn't pull the EN pin low by default? Anyways, I'll close this issue soon and create a section for Troubleshooting, where I'll link to this issue.

Dytoractor, 2025-04-18:
I tried to save money and use my old 2209 v1.2 and I ran into the same issue where my motors were not turning. Thank you Nik for showing me this fix!!! It worked! However, I don't have enough v1.2's for the other two units I am making for my nieces. So I ended up buying four V1.3 drivers.

Curious, does it hurt to just always put the ENN Pin in? no matter which driver  it is. Like the picture I made

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

nikivanov, 2025-04-18:
It shouldn't hurt to have the EN pin be connected. Maybe some variants of tmc2209 has En pin floating voltage be high enough to considered high. I'll add a note about it. Thanks!

Dytoractor, 2025-04-19:
Sorry, one more question!

Where do you find your SVG files? or do you have a forum/ "how to" page on
this?
I tried to make some but they ended up being "pictures". I found some free
svg's online that have gcode when you open them and they work... I found
this border (attached). but none of the other svg's show up in the
preview.

thank you

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

nikivanov, 2025-04-20:
@Dytoractor there's https://freesvg.org/ , I also had decent luck with just typing in what i want with "svg free" in google. Also, as @AMagill recommended, you can ask an AI generator to "create a vector image of [your prompt], line art" and then have it traced using InkScape or potrace

JesusBoraita, 2025-07-18:
@Dytoractor I had the same problem with the motors not moving with TMC 2209 v2.0 drivers. This schematic saved the day by connecting the enable pin. Thank you all so much for your work and effort.

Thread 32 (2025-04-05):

Calibration ?

jp3141, 2025-04-05:
What is required for position calibration ? Obviously you don't pull the cables until they are horizontal -- is there a 'top of print' angle or distance from the support points ?

nikivanov, 2025-04-05:
The belts are placed on homing bolts so the initial belt length is known. After that Mural just assumed no steps are skipped.

nikivanov, 2025-04-05:
Oh I don't think that was your question. Mural's drawing margins are 20% from the top and 20% from each side, taken from the distance between the hangers.

jp3141, 2025-04-06:
Yes. That was my Q. I always skipped that step since the ends of the belts are high and inaccessible 🙃. I understand now...  thanks. John--John PigottOn Apr 5, 2025, at 16:35, Nik Ivanov ***@***.***> wrote:
  The belts are placed on homing bolts so the initial belt length is known. After that Mural just assumed no steps are skipped.—Reply to this email directly, view it on GitHub, or unsubscribe.You are receiving this because you authored the thread.Message ID: ***@***.***>

nikivanov left a comment (nikivanov/mural#32)
The belts are placed on homing bolts so the initial belt length is known. After that Mural just assumed no steps are skipped.

—Reply to this email directly, view it on GitHub, or unsubscribe.You are receiving this because you authored the thread.Message ID: ***@***.***>

Closed 2025-04-06.

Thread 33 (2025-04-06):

Scaling issues during preview

mrdavidgagnon, 2025-04-06:
For any .svg I select, the move and resize screen looks great, but then the preview screen shrinks the image and moves it to the top left corner. The print also comes out small.

FWIW,Thank you for sharing this incredible project!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

nikivanov, 2025-04-06:
Could you please attach the original SVG?

mrdavidgagnon, 2025-04-06:
New insight! The problem went away when I switched to my desktop Mac computer running Chrome. It seems there is an issue with desktop and mobile safari.

nikivanov, 2025-04-06:
Good to know! I've done 0 testing on safari, Chrome is currently the only supported browser.

StefanMeGit, 2025-04-22:
It would be incredible helpfull when you are able to tell the approximate dimensions of the drawing instead of the "scale factor". 0.X is absolute useless for me... but 1000mm in width would be a great hint how big the drawing would be on the wall.

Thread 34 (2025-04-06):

Distortion Correction Fix!

TheSeanLavery, 2025-04-06:
I made a fork of your repo. It corrects the distortion and has adjustable parameters to tweak the correction.

I also built a python based plotter simulator to understand the distortion, and visualize the corrections.

I did this under an hour from seeing your video. Here is the repo https://github.com/TheSeanLavery/mural/tree/distortion-correction

Not sure if it will work 1st try on a real device, but I think this can solve the issue, and it did compile with out errors.

nikivanov, 2025-04-08:
Thanks for making these changes! The main issue is that I'm not really sure where the distortion is. I need to draw a calibration grid with Mural and then manually draw the geometrically accurate version of the same grid with a big ruler. Once I can quantify the distortion, correcting it should be as easy as applying a matrix to the drawing coordinates.

I initially hoped that somebody would know how to accurately model Mural's movement in code, catenary curves and all, but the general consensus so far is that dewarping is the easiest approach.

TheSeanLavery, 2025-04-08:
I think I may actually be modeling Mural's movement with the python visualizer.

If its not doing what it should be doing. I can see about correcting this an alternate way.

You may not need to even run a calibration with my code here.

I don't have a device yet. So I'm unable to test with real hardware.

nikivanov, 2025-04-09:
You're modeling Mural's movements as Mural perceives them to be - same code as in movement.cpp. Mural's input is (x,y) coordinates and output is belt lengths. The issue is that when Mural accepts desired (x,y) coordinates, it converts them to belt lengths, but the actual (x,y) you end up with on the wall are different from the original desired (x,y) coordinates.

As I mentioned above, there are two ways to approach this: model the movement correctly (which I don't know how to do), or use a dewarping matrix by drawing a grid using Mural and then superimposing the same geometrically-correct grid onto it - the resulting matrix can be used to warp the original coordinates to shoehorn Mural's sort-of-incorrect movement model into drawing geometrically-correct images.

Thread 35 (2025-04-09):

Keeps drawing the wrong image

AMagill, 2025-04-09:
Today I tried drawing this, but it was just coming out as complete mess.  (I'll be looking forward to the render mode that just traces SVG lines without the whole vector-to-raster-to-vector process.  finitecurve.com will be great for this then!)

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

So, I pulled the plug and started over with a different SVG.  Previews looked good through the whole setup process, but then it started drawing the first image again!  So again I unplugged it, took it down, retracted the belts, plugged it back in, this time used Chrome instead of Firefox to go through setup again, loaded the new SVG, made sure the previews were correct, started.. and it's drawing the first image for a third time.

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

I guess the old vector data isn't getting cleared from the device if it doesn't run to completion, even if you power cycle and start a whole new drawing?

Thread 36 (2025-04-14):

[Question] Motors temperature

kivson, 2025-04-14:
Hi, thanks for the amazing project.

I just finished my first draw (10 min duration) and the motors are really hot,
barely can touch them for a second. Is that normal?

Only thing I did different from the assembly video was that my reference voltage between the adjustment screw and grd was already at 1.1 volts, so did no adjustment there. Any suggestion on how reduce the temperature?

nikivanov, 2025-04-15:
In my experience, motors do get hot to the point where you cant hold them, but that doesnt seem to affect performance. One of the members on the discord server suggested I use UART as the interface method between the microcontroller and the driver - it should eliminate the need for setting VREF too. This wouldn't require any new parts, but would slightly change the wiring.

depthpicker, 2025-04-27:
Hi first of all congratulations and thanks for this cool project!
If I may, I would like to share a few observations on the matter of the heat issue. I built this project and have observed significant thermal differences between the mural firmware and my own esp32 code that I run on the same hardware..

It appears that when running the mural firmware with VREF set to a low value of 0.75V, the motors consistently reached temperatures of approximately 50°C, even during periods of inactivity or when not even mounted against a wall. At 1V they get even hotter. With my own simple esp32 code (just a web interface and buttons to manually drive the motors also using Step Dir ), the motors stay cool to the touch. However, upon reverting to the original mural firmware, the elevated temperature issue immediately returned..

nikivanov, 2025-04-27:
Are you willing to share your code so I can compare?

nikivanov, 2025-05-14:
Motors stay energized so they hold position at all times. If your firmware moves them and then disables them, that doesn't really count

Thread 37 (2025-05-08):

TMC2209 IO logic 5V instead of 3.3V

analogic, 2025-05-08:
Hi Nik, I don't have exactly the same parts as you recommend as I have almost all the parts in house but in slightly different versions. It happens that I have already fried two esp32s and the steppers are still not moving properly. So I have to dig deeper

I found some discrepancies in the video. Should the TMC2209 extension board be connected to the 3.3V from the ESP32 rather than the 5V source - AFAIK it is connected to VCC_IO and the ESP32 outputs 3.3V?

analogic, 2025-05-09:
I would expect VCC_IO to define the voltage level of the IO logic, so if the ESP32 outputs a lower voltage it could potentially cause problems in some extreme cases...

nikivanov, 2025-05-09:
I see what you're saying, but it seems that powering tmc2209 with 5v and then using 3.3v to control step and for just works, for whatever reason, for quite a lot of people.

For your immediate problem, have you tried https://github.com/nikivanov/mural/issues/31 ?

nikivanov, 2025-05-10:
Yeah that looks like it has everything you'd need. Let me know how the port
goes!

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

CCERocks, 2025-05-14:
Hi @analogic & @nikivanov, my FYSETC E4 board just arrive today & I'm flash with getmural firmware... Unfortunately only RIGHT MOTOR is working.

Any guide to make the LEFT MOTOR working too?

Anyway @nikivanov would you add option to speed?

nikivanov, 2025-05-14:
You can modify drawing speed here: https://github.com/nikivanov/mural/blob/4682db1fa4d548cf25d1176ae29ae6e4425b6ff8/src/movement.h#L6

As for the board, I don't have one and have never used it so I can't provide support for it. I'll keep the issue open in case @analogic gets it to work

CCERocks, 2025-05-15:
this is your setting for motor pin

const auto LEFT_STEP_PIN = 13;
const auto LEFT_DIR_PIN = 12;
const auto LEFT_ENABLE_PIN = 14;

const auto RIGHT_STEP_PIN = 27;
const auto RIGHT_DIR_PIN = 26;
const auto RIGHT_ENABLE_PIN = 25;

For FYSETC E4

X-MOTOR(1)  <--- RIGHT MOTOR
X-Step | 27  
X-DIR | 26  
X-EN | 25

Y-MOTOR(2) <--- LEFT MOTOR ? so should follow this FYSETC info to your movement.h right?
Y-Step | 33
Y-DIR | 32
Y-EN | 25
 
Z-MOTOR(3)
Z-Step | 14
Z-DIR | 12
Z-EN | 25

E0-MOTOR(4)
E0-Step | 16
E0-DIR | 17
E0-EN | 25

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

but which pin for Servo ? using Endstops, pin 34, 35, 15 or FAN pin 13 ?

nikivanov, 2025-05-15:
Yep, if you connect the left motor to the Y motor connector, you just need to use those pins from Fysetc E4 spec

CCERocks, 2025-05-16:
> Yep, if you connect the left motor to the Y motor connector, you just need to use those pins from Fysetc E4 spec

Pin 17 for Servo?

Well I have to redesign the casing to fit the new board. Maybe motor can be put this way... Since nothing at that area.

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

nikivanov, 2025-05-17:
You can use any of the pins that support PWM (that's most of them, but depends on the exact esp32 chip type). Pick a pin from the available list that isn't already used and that supports PWM, plug the servo into that and modify the pin number here: https://github.com/nikivanov/mural/blob/main/src/pen.cpp#L49

CCERocks, 2025-05-18:
> You can use any of the pins that support PWM (that's most of them, but depends on the exact esp32 chip type). Pick a pin from the available list that isn't already used and that supports PWM, plug the servo into that and modify the pin number here: https://github.com/nikivanov/mural/blob/main/src/pen.cpp#L49

Noted. Thank you for the info...

Anyway.. its would be a great upgrade to have option to choose speed either with slider or numeric input or even by percentage anywhere in the MURAL Interface.. or just put it inside setting when user can see how fast the motor spin..

😅

nikivanov, 2025-05-18:
I hear you, but I wanted to provide the user with "just works" experience. If the drawing speed can be altered, I need to find the min and the max through testing, and I don't have the time. You're welcome to modify the speed in the firmware and flash it on your Mural. If you can confirm higher speeds without sacrifice in quality, please let me know!

CCERocks, 2025-05-25:
> The motors work flawlessly this time! The servo seems to be a bit of a problem – the board itself only has an AMS1117, which does not have enough power to feed the ESP32 and the servo, so a step-down converter from 12V to 5V needs to be used. The SDA/SCL pins (22 and 21) should work to control the ESP32 (on the 3x4 header close to it). I'll try it later. I am also kind of tempted to change the servo to a stepper with code doing a similar thing.

well.. there isa  small stepper motor 28BYJ-48 have 12V version... maybe can use this one without any conversion ?

analogic, 2025-05-28:
A few notes:
- For the servo, I used a Mini360 step-down converter in a heat-shrink tube, which I connected to the hotbed screw terminal. You need to set pin 4 to HIGH before doing anything else.
- To drive the servo, I use the SCL board pin (pin 22 internally, near the ESP32 board).
- The TMC2209s are meant to be commanded by UART on this board (MS1 and MS2 are used for the address, not for microstepping), so some additional code is required to set the same values for the microsteps; otherwise, one will rotate faster.
- Also, the holding current must be set via UART to prevent the motor from getting unnecessarily hot.

CCERocks, 2025-05-30:
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

Would you mind sharing your source code?... I can share you my Mural case design that fit this FYSETC E4 board... 😂 Notes.. it's different.

nikivanov, 2025-05-30:
We're talking on github - the source code is all here :) What are you looking for specifically? If it's the STEP file for Mural, it's here: https://github.com/nikivanov/mural/blob/main/STLs/Mural.step

CCERocks, 2025-05-31:
> ~~We're talking on github - the source code is all here. What are you looking for specifically? If it's the STEP file for Mural, it's here: https://github.com/nikivanov/mural/blob/main/STLs/Mural.step~~
>
> Ah, sorry, I think you were asking @analogic

LoL... It's ok... I will eventually share the design of your Mural that use FYSTEC board if I get the code correctly. 😀

analogic, 2025-06-04:
Ok, now I've test code for the board and working motors. I'll try to implement to mural code later

Test code:
```
#include <Arduino.h>
#include <TMCStepper.h>
#include <ESP32Servo.h>
#include <AccelStepper.h>

#define LED_BUILTIN 2 // blinking with FAN led

#define SERIAL_RX     21    // PDN_UART → RX2
#define SERIAL_TX     22    // PDN_UART → TX2

#define SERVO_PWR_PIN 4

#define EN_PIN 25

#define STEP_PIN_1 27 // Motor 1 STEP pin
#define DIR_PIN_1 26  // Motor 1 DIR pin

#define STEP_PIN_3 33 // Motor 3 STEP pin
#define DIR_PIN_3 32  // Motor 3 DIR pin

#define SERVO_PIN 15 // Servo motor pin

#define R_SENSE 0.22f

Servo servo;

HardwareSerial tmcSerial(2);

TMC2209Stepper drv1(&tmcSerial, R_SENSE, 1);
TMC2209Stepper drv3(&tmcSerial, R_SENSE, 3);

AccelStepper stepper1(AccelStepper::DRIVER, STEP_PIN_1, DIR_PIN_1);
AccelStepper stepper3(AccelStepper::DRIVER, STEP_PIN_3, DIR_PIN_3);

void fatalError()
{
    Serial.println("Fatal error occurred. Stopping execution.");
    pinMode(LED_BUILTIN, OUTPUT);
    while (1) {
        digitalWrite(LED_BUILTIN, HIGH);
        delay(500);
        digitalWrite(LED_BUILTIN, LOW);
        delay(500);
    }
}

void setup()
{
    Serial.begin(115200);
    while (!Serial);

    tmcSerial.begin(115200, SERIAL_8N1, SERIAL_RX, SERIAL_TX);
    while (!tmcSerial);

    pinMode(STEP_PIN_1, OUTPUT);
    pinMode(DIR_PIN_1, OUTPUT);
    pinMode(STEP_PIN_3, OUTPUT);
    pinMode(DIR_PIN_3, OUTPUT);

    pinMode(EN_PIN, OUTPUT);
    digitalWrite(EN_PIN, LOW);

    pinMode(SERVO_PWR_PIN, OUTPUT);
    digitalWrite(SERVO_PWR_PIN, HIGH);

    auto version1 = drv1.version();
    if (version1 != 0x21) {
        Serial.println("Driver 1 version mismatch!");
        Serial.println("Expected version 0x21, got: " + String(version1, HEX));
        fatalError();
    }
    auto version3 = drv3.version();
    if (version3 != 0x21) {
        Serial.println("Driver 3 version mismatch!");
        Serial.println("Expected version 0x21, got: " + String(version3, HEX));
        fatalError();
    }

    drv1.toff(5); // Enable driver
    drv1.rms_current(400); // Lower RMS current (example: 400mA)
    drv1.mstep_reg_select(true); // Enable microsteps via UART
    drv1.microsteps(16);
    drv1.push();

    drv3.toff(5);
    drv3.rms_current(400);
    drv1.mstep_reg_select(true); // Enable microsteps via UART
    drv3.microsteps(16);
    drv3.push();

    // Configure stepper 1
    stepper1.setMaxSpeed(1000); // Set maximum speed (steps per second)
    stepper1.setAcceleration(500); // Set acceleration (steps per second^2)
    stepper1.moveTo(3200); // Move one full revolution (example: 200 steps/rev * 16 microsteps)

    while (stepper1.distanceToGo() != 0) {
        stepper1.run(); // Run stepper 1
    }

    // Configure stepper 3
    stepper3.setMaxSpeed(1000); // Set maximum speed (steps per second)
    stepper3.setAcceleration(500); // Set acceleration (steps per second^2)
    stepper3.moveTo(3200); // Move one full revolution (example: 200 steps/rev * 16 microsteps)

    while (stepper3.distanceToGo() != 0) {
        stepper3.run(); // Run stepper 3
    }

    servo.attach(SERVO_PIN); // Attach servo motor to pin 21

    for (int i = 0; i < 3; i++) { // Repeat the movement three times
        servo.write(90); // Move to 90 degrees (open position)
        delay(1000);     // Wait for ~1 second to ensure movement completes

        // Test closing functionality
        servo.write(0); // Move to 0 degrees (closed position)
        delay(1000);    // Wait for ~1 second to ensure movement completes
    }

    servo.detach(); // Stop sending signals to the servo

}

void loop()
{
}
```

Wiring (servo motor is from z-min pin, power is from hotbead and converted to 5v with mini360):

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

analogic, 2025-06-06:
https://github.com/analogic/mural - Here is fork with settings implemented - it is working but not yet fully tested.

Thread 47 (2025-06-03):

Mural crashes at the end of drawing

schmidt3d, 2025-06-03:
This is a minor issue, but wanted to bring it up anyways because it interferes a bit with debugging: I noticed that Mural crashes when it finishes the drawing.
From the log:

```
...
Pen task is done
Starting the move to 0.000000, 150.000000
Starting the move to 150.000000, 150.000000
Starting the move to 300.000000, 150.000000
Starting the move to 300.000000, 75.000000
Starting the move to 300.000000, 0.000000
Starting the move to 150.000000, 0.000000
Starting the move to 0.000000, 0.000000
Starting the move to 0.000000, 75.000000
Starting pen task 1
Pen is going up
Pen task ran
Pen task is done
Starting the move to 150.000000, 350.000000
ق�gݵ�1�H6��1��
�Initialized display
Initialized steppers
*wm:AutoConnect
*wm:Connecting to SAVED AP: terelj
*wm:AutoConnect: SUCCESS
*wm:STA IP Address: 192.168.0.232
Connected to wifi
Started mDNS for mural
Initialized servo
Initialized runner
Finished setting up the server
Switching current phase to SetTopDistance
Server started
...
```

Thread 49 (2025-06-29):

Belt slipping / stepper motor under powered

adisharmagit, 2025-06-29:
Hello All,

First post and first project with 3d printed parts.

Since I borrowed 3d printer, i got the files printed on PLA. I see an issue where the belt slips when hung. Without weight, when the mural is in hand, the belt runs fine. When the belt slips, it seems like the gear is also stuck (i am just hearing motor clicks.) thus i think maybe it's under powered?

This is my first time using a stepper motor. I see the motor is extremely quiet and gets very hot (based on other posts that expected)

Since the recommended motor in the bom was not available, i am using the following motor.

https://www.amazon.com/dp/B07TNPCWGK?ref=ppx_yo2ov_dt_b_fed_asin_title&th=1
Usongshine Nema 17 Stepper Motor Bipolar Step Motor for Titan Extruder 3D Printer 4.1V 1A 13Ncm

Recommend power supply was also not available thus I am using following. The supply is rated for 3amps at 12V thus I think it does have power
45W Super Fast Charger Type... https://www.amazon.com/dp/B0CNGVPT22?ref=ppx_pop_mob_ap_share

Thanks again for the awesome project, i built it with my 6-year-old son, who is extremely excited to see it work real-time.

Thanks for help

nikivanov, 2025-07-04:
I've never used these motors but they are rated for 1A, and Mural runs at 0.8A, so it should be ok. Did you set your VRef correctly to 1.1V like in the video?

The power supply should be ok at 3A

adisharmagit, 2025-07-10:
Yes, the ref voltage is set for 1.1v i also found the power brick was not supplying as written causing mural to stop. I switched to new anker 45W power supply which keeps it running but I still see belts slips. Wondering what others are using for motors as twotree motors are not available anymore.

adisharmagit, 2025-07-11:
Thanks for checking, I finally gave up replaced the right stepper motor, which was mainly clicking, and it works now. I also believe my previous power supply was not actually supplying the 3A current at 12V and thus causing other issues.

Thanks again for the awesome project! I had fun building this with my son

nikivanov, 2025-07-11:
Great! I'll close the issue then.

Closed 2025-07-11.

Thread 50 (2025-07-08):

Investigating MKS DLC32

Sutto, 2025-07-08:
I built an initial mural (I love the project btw!) using some tweaked hardware - due to what was on hand and budget considerations. Hot glue went a long way to making some of the pieces a fit without modification.

Now, in doing so - I wondered if we had another option to make the process even easier - CNC boards based on the ESP32 of different varieties are quite common, and if we're sourcing from Aliexpress, super cheap.

In particular, the form factor, features and price of one boar in particular stood out to me - the Makerbase MKS DLC32.

Feature wise, it support:

* 3x Stepper motor drivers (no need for seperate boards to for each powered off the ESP32).
* Built in step down regulators, and designed for the higher power requirements of driving these motors.
* Compact form factor, with plenty of IO
* Easy USB connection etc lie the standard DevKit design.

And as of talking, I've found the whole board pretty available around the $22 AUD mark - bargain!

The only limiting factor to a straight port (adjust pins etc) appears to be the use of I2S as a novel way of driving the motor drivers / to expand GPIO's: https://github.com/bdring/Grbl_Esp32/blob/main/Grbl_Esp32/src/I2SOut.cpp

To this end, I've got a board on hand and plan to dive into the code this weekend / over the next few weeks to see what would be required to adjust it. It'll also make assembly much, much easier - and I'd just have to adjust the hanger design.

I'll drop some comments here as I investigate it more :)

flow1986, 2025-07-21:
i had the same idea with the MKS-DLC32 board:

https://github.com/nikivanov/mural/issues/22

i don´t have the time to investigate further, so i much appreciate your work and hope you can reprogram the code to use with the MKS-DLC32.

thanks a lot!

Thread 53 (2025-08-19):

Max drawing size?

HippoDan, 2025-08-19:
I'm trying to draw a large image. However anytime I use a distance between the nails of greater than about 1600mm it will crash on preview even for a simple item like a square.

Based on the taking 20% from the three sides. I need the nails at least 2,000 mm apart.

HippoDan, 2025-08-27:
Chrome for android.  I can try again from my laptop.

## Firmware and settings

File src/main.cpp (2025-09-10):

#include <Arduino.h>
#include <WiFiManager.h>
#include <AsyncTCP.h>
#include <ESPAsyncWebServer.h>
#include <FS.h>
#include <LittleFS.h>
#include <Wire.h>
#include <ESPmDNS.h>
#include "movement.h"
#include "runner.h"
#include "pen.h"
#include "display.h"
#include "phases/phasemanager.h"

AsyncWebServer server(80);

Movement *movement;
Runner *runner;
Pen *pen;
Display *display;

PhaseManager* phaseManager;

void notFound(AsyncWebServerRequest *request)
{
    request->send(404, "text/plain", "Not found");
}

void handleUpload(AsyncWebServerRequest *request, String filename, size_t index, uint8_t *data, size_t len, bool final) {
    phaseManager->getCurrentPhase()->handleUpload(request, filename, index, data, len, final);
}

void handleGetState(AsyncWebServerRequest *request) {
    phaseManager->respondWithState(request);
}

std::vector<const char *> menu = {"wifi", "sep"};
void setup()
{
    delay(10);
    Serial.begin(9600);

    if (!LittleFS.begin(true)) {
        Serial.println("An Error has occurred while mounting LittleFS");
        return;
    }

    display = new Display();
    Serial.println("Initialized display");

    // initialize movement right away or the motors can start creeping due to floating output
    movement = new Movement(display);
    Serial.println("Initialized steppers");

    bool resetAfterConnect = false;
    std::function<void()> serverCallback = [&] () {
        resetAfterConnect = true;
    };
    
    WiFiManager wifiManager;
    
    wifiManager.setConnectTimeout(20);
    wifiManager.setTitle("Connect to WiFi");
    wifiManager.setMenu(menu);
    wifiManager.setWebServerCallback(serverCallback);
    wifiManager.autoConnect("Mural");

    if (resetAfterConnect) {
        Serial.println("Connected to WiFi through captive portal, restarting...");
        ESP.restart();
    }
    
    Serial.println("Connected to wifi");

    MDNS.begin("mural");

    Serial.println("Started mDNS for mural");

    pen = new Pen();
    Serial.println("Initialized servo");

    runner = new Runner(movement, pen, display);
    Serial.println("Initialized runner");

    server.serveStatic("/", LittleFS, "/www/").setDefaultFile("index.html").setCacheControl("no-cache");

    server.on("/command", HTTP_POST, [](AsyncWebServerRequest *request)
              { phaseManager->getCurrentPhase()->handleCommand(request); });

    server.on("/setTopDistance", HTTP_POST, [](AsyncWebServerRequest *request)
              { phaseManager->getCurrentPhase()->setTopDistance(request); });

    server.on("/extendToHome", HTTP_POST, [](AsyncWebServerRequest *request)
              { phaseManager->getCurrentPhase()->extendToHome(request); });

    server.on("/setServo", HTTP_POST, [](AsyncWebServerRequest *request)
              { phaseManager->getCurrentPhase()->setServo(request); });

    server.on("/setPenDistance", HTTP_POST, [](AsyncWebServerRequest *request)
              { phaseManager->getCurrentPhase()->setPenDistance(request); });

    server.on("/estepsCalibration", HTTP_POST, [](AsyncWebServerRequest *request)
              { phaseManager->getCurrentPhase()->estepsCalibration(request); });

    server.on("/doneWithPhase", HTTP_POST, [](AsyncWebServerRequest *request)
              { phaseManager->getCurrentPhase()->doneWithPhase(request); });

    server.on("/run", HTTP_POST, [](AsyncWebServerRequest *request)
              { phaseManager->getCurrentPhase()->run(request); });

    server.on("/resume", HTTP_POST, [](AsyncWebServerRequest *request)
              { phaseManager->getCurrentPhase()->resumeTopDistance(request); });

    server.on("/getState", HTTP_GET, [](AsyncWebServerRequest *request)
              { handleGetState(request); });

    server.on(
        "/uploadCommands", HTTP_POST,
        [](AsyncWebServerRequest *request) {
            handleGetState(request);
        }, 
        handleUpload
    );

    server.on(
        "/downloadCommands", HTTP_GET,
        [](AsyncWebServerRequest *request) {
            request->send(LittleFS, "/commands", "text/plain");
        }
    );

    server.onNotFound(notFound);

    Serial.println("Finished setting up the server");

    phaseManager = new PhaseManager(movement, pen, runner, &server);

    server.begin();
    Serial.println("Server started");

    display->displayHomeScreen("http://" + WiFi.localIP().toString(), "or", "http://mural.local");
    
}

void loop()
{
    movement->runSteppers();
    runner->run();
    phaseManager->getCurrentPhase()->loopPhase();
}

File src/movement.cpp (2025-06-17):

#include "movement.h"
#include "display.h"
#include <stdexcept>

Movement::Movement(Display *display)
{
    this->display = display;
   
    leftMotor = new AccelStepper(AccelStepper::DRIVER, LEFT_STEP_PIN, LEFT_DIR_PIN);
    leftMotor->setEnablePin(LEFT_ENABLE_PIN);
    leftMotor->setMaxSpeed(moveSpeedSteps);
    leftMotor->setPinsInverted(true);
    leftMotor->disableOutputs();

    rightMotor = new AccelStepper(AccelStepper::DRIVER, RIGHT_STEP_PIN, RIGHT_DIR_PIN);
    rightMotor->setEnablePin(RIGHT_ENABLE_PIN);
    rightMotor->setMaxSpeed(moveSpeedSteps);
    rightMotor->disableOutputs();

    topDistance = -1;
   
    moving = false;
    homed = false;
    startedHoming = false;
};

void Movement::setTopDistance(const int distance) {
    Serial.printf("Top distance set to %s\n", String(distance));
    topDistance = distance;                         // = d_pins [mm]

    minSafeY = safeYFraction * topDistance;         // = top_margin * d_pins [mm]
    minSafeXOffset = safeXFraction * topDistance;   // = side_margin * d_pins [mm]
    width = topDistance - 2 * minSafeXOffset;       // width of the drawing area [mm]
};

void Movement::resumeTopDistance(int distance /* = d_pin in mm */) {
    setTopDistance(distance);
    homed = true;

    const Point homeCoordinates = getHomeCoordinates();
    X = homeCoordinates.x;
    Y = homeCoordinates.y;

    const Lengths lengths = getBeltLengths(homeCoordinates.x, homeCoordinates.y);
    leftMotor->setCurrentPosition(lengths.left);
    rightMotor->setCurrentPosition(lengths.right);

    moving = false;
}

void Movement::setOrigin()
{
    leftMotor->setCurrentPosition(homedStepsOffset);
    rightMotor->setCurrentPosition(homedStepsOffset);
    homed = true;
};

void Movement::leftStepper(const int dir)
{
    if (dir > 0)
    {
        leftMotor->move(INFINITE_STEPS);
        leftMotor->setSpeed(printSpeedSteps);
    }
    else if (dir < 0)
    {
        leftMotor->move(-INFINITE_STEPS);
        leftMotor->setSpeed(printSpeedSteps);
    }
    else
    {
        leftMotor->setAcceleration(acceleration);
        leftMotor->stop();
    }

    moving = true;
};

void Movement::rightStepper(const int dir)
{
    if (dir > 0)
    {
        rightMotor->move(INFINITE_STEPS);
        rightMotor->setSpeed(printSpeedSteps);
    }
    else if (dir < 0)
    {
        rightMotor->move(-INFINITE_STEPS);
        rightMotor->setSpeed(printSpeedSteps);
    }
    else
    {
        rightMotor->setAcceleration(acceleration);
        rightMotor->stop();
    }

    moving = true;
};

Movement::Point Movement::getHomeCoordinates() {
    if (topDistance == -1) {
        return Point(0, 0);
    }

    return Point(width / 2, HOME_Y_OFFSET_MM);
}

int Movement::extendToHome()
{
    setOrigin();

    auto homeCoordinates = getHomeCoordinates();
    startedHoming = true;
    auto moveTime = beginLinearTravel(homeCoordinates.x, homeCoordinates.y, moveSpeedSteps);
    return int(ceil(moveTime));
};

void Movement::runSteppers()
{
    if (moving)
    {
        leftMotor->runSpeedToPosition();
        rightMotor->runSpeedToPosition();

        if (leftMotor->distanceToGo() == 0 && rightMotor->distanceToGo() == 0)
        {
            moving = false;
            //Serial.printf("Motion complete. Left steps: %ld, Right steps: %ld\n", leftMotor->currentPosition(), rightMotor->currentPosition());
        }
    }
};

inline void Movement::getLeftTangentPoint(const double frameX, const double frameY, const double gamma, double& x_PL, double& y_PL) const {
    // Input frameX and frameY are the coordinates of the pen center.
    const double s_L = d_t / 2.0;   // Distance of left and right tangent point from point Q. [mm]
    const double P_LX = s_L * cos(gamma) - d_p * sin(gamma); // [mm] distance from pen center in x
    const double P_LY = s_L * sin(gamma) + d_p * cos(gamma); // [mm] .. and y
    x_PL = frameX - P_LX;    // [mm] Left pulley tangent point in frame coordinate system.
    y_PL = frameY - P_LY;    // [mm]
}

inline void Movement::getRightTangentPoint(const double frameX, const double frameY, const double gamma, double& x_PR, double& y_PR) const {
    // Coordinates of right pulley tangent point:
    const double s_R = d_t / 2.0;
    const double P_RX = s_R * cos(gamma) + d_p * sin(gamma); // [mm]
    const double P_RY = s_R * sin(gamma) - d_p * cos(gamma); // [mm]
    x_PR = frameX + P_RX;    // [mm] Right pulley tangent point in frame coordinate system.
    y_PR = frameY + P_RY;    // [mm]
}

// Compute angles of the belts and the forces on them.
// Input: - Mural coordinates X and Y in frame coordinate system [mm].
//        - Mural inclination gamma [rad].
// Output: - belt angles phi_L, phi_R [rad], measured against the line connecting the pins.
void Movement::getBeltAngles(const double frameX, const double frameY, const double gamma, double& phi_L, double& phi_R) const {
    double x_PL;
    double y_PL;
    getLeftTangentPoint(frameX, frameY, gamma, x_PL, y_PL);
    phi_L = atan2(y_PL, x_PL);     // Angle of left belt, measured from line connecting the pins. [rad]

    double x_PR;
    double y_PR;
    getRightTangentPoint(frameX, frameY, gamma, x_PR, y_PR);
    phi_R = atan2(y_PR, topDistance - x_PR);     // Angle of left belt, measured from line connecting the pins. [rad]
}

void Movement::getBeltForces(const double phi_L, const double phi_R, double& F_L, double&F_R) const {
    // Computing the Forces. 
    // Force vectors are parallel to their belts, so the direction is given by phi_R and phi_L.
    // We assume that the bot is in a stable state (no torque), which allows us for having
    // the force vectors of left (L) and right (R) pulley meet in a single point. 
    // In this stable state the pulley forces cancel out the gravity force in x and y.
    // Note this is an approximation which is refined due to iteratively updating the values (torque, angles, forces). 
    const double F_G = mass_bot * g_constant;       // [N] Gravity force is pulling bot down. No x component.
    F_R = F_G * cos(phi_L) / sin(phi_L + phi_R);    // [N] magnitude of the force vector
    F_L = F_G * cos(phi_R) / sin(phi_L + phi_R);    // [N]
    // double F_Ly = F_L * sin(phi_L);                         // [N] components in y and x
    // double F_Lx = F_L * sin(phi_L);                         // [N] ...
    // double F_Ry = F_R * sin(phi_R);                         // [N]
    // double F_Rx = F_R * sin(phi_R);                         // [N]
}
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

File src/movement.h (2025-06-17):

#ifndef Movement_h
#define Movement_h

#include "AccelStepper.h"
#include "Arduino.h" 
#include "display.h"

// Motor driver parameters.
constexpr int printSpeedSteps = 500;
constexpr int  moveSpeedSteps = 1500;
constexpr long INFINITE_STEPS = 999999999;
constexpr long acceleration = 999999999;  // Essentially infinite, causing instant stop / start
constexpr int stepsPerRotation = 200 * 8; // 1/8 microstepping

// Geometry parameters:
// Effective diameter of the pulley+belts. Use EStep calibration to refine this value.
constexpr double diameter = 12.69;          // [mm]
const double circumference = diameter * PI; // [mm]
constexpr double midPulleyToWall = 41.0;    // (Height) distance from mid of pulley to wall [mm].
constexpr float homedStepOffsetMM = 40.0;   // Length of fully retracted belt hitting stop screw.
                                            // Measured from outer edge of screw to the point
                                            // of tangency between belt and pulley. [mm]
const int homedStepsOffset = int((homedStepOffsetMM / circumference) * stepsPerRotation);
constexpr double mass_bot = 0.55;   // Mass of the mural bot [kg].
constexpr double g_constant = 9.81; // Earth's gravitational acceleration constant [m/s^2]. Please adjust when running Mural on other planets!
constexpr double d_t = 76.027;      // [mm] Distance of tangent points, where belts touch the pulleys.
                                    // Calculated as (axis distance) 85.00 - (diameter) 12.69/sqrt(2).
constexpr double d_p = 4.4866;      // [mm] distance from Q to center of pen. Calculated as diameter/(2 * sqrt(2)).
constexpr double d_m = 10.0 + d_p;  // [mm] Distance from line connecting tangent points to center of mass of bot (projected onto wall plane).
                                    // The point where d_m and d_t meet shall be called Q.
                                    // The center of mass sits roughly at the bottom of the pen opening.
constexpr double belt_elongation_coefficient = 5e-5; // [m/N] elongation of the belts under force.
const int HOME_Y_OFFSET_MM = 350;   // Y coordinate of mural home position in image coordinate system [mm].


// Margins used for transformations of the coordinate systems:
constexpr double safeYFraction = 0.2;           // Top Margin: Image top to topDistance line.
constexpr double safeXFraction = 0.2;           // Left and right margin: from draw area boundaries to line from each pin straight down.

// Variables used for debugging:
// constexpr int sleepDurationAfterMove_ms = 0;    // Delay after linear movement [ms], e.g. 50.

// ESP setup:
constexpr int LEFT_STEP_PIN = 13;
constexpr int LEFT_DIR_PIN = 12;
constexpr int LEFT_ENABLE_PIN = 14;

constexpr int RIGHT_STEP_PIN = 27;
constexpr int RIGHT_DIR_PIN = 26;
constexpr int RIGHT_ENABLE_PIN = 25;

class Movement{
private:
    int topDistance;            // Distance between pins (d_pins) [mm].
    double minSafeY;
    double minSafeXOffset;
    double width;               // width of the drawing area [mm]
    volatile bool moving;
    bool homed;
    double X = -1;              // Location of Pen in x [mm].
    double Y = -1;              // Location of Pen in y [mm].
    bool startedHoming;
    AccelStepper *leftMotor;
    AccelStepper *rightMotor;
    Display *display;
    void setOrigin();

    struct Lengths {
        int left;
        int right;
        Lengths(int left, int right) {
            this->left = left;
            this->right = right;
        }
        Lengths() {

        }
    };

    Lengths getBeltLengths(double x, double y);

    double gamma_last_position = 0.0;   // [rad] The last known inclination of the mural bot. As the angle changes only slowly 
                                        // with position we can compute updates faster by keeping track of the last solution.
    inline void getLeftTangentPoint(const double frameX, const double frameY, const double gamma, double& x_PL, double& y_PL) const;
    inline void getRightTangentPoint(const double frameX, const double frameY, const double gamma, double& x_PR, double& y_PR) const;
    void getBeltAngles(const double frameX, const double frameY, const double gamma, double& phi_L, double& phi_R) const;
    void getBeltForces(const double phi_L, const double phi_R, double& F_L, double&F_R) const;
    double solveTorqueEquilibrium(const double phi_L, const double phi_R, const double F_L, const double F_R, const double gamma_start) const;
    double getDilationCorrectedBeltLength(double belt_length, double F_belt) const;
    
public:
    Movement(Display *display);
    struct Point {
        double x;
        double y;
        Point(double x, double y) {
            this->x = x;
            this->y = y;
        }
        Point() {
        }
    };

    static double distanceBetweenPoints(Point point1, Point point2) {
        return sqrt(pow(point2.x - point1.x, 2) + pow(point2.y - point1.y, 2));
    }

    bool isMoving();
    bool hasStartedHoming();
    double getWidth();
    Point getCoordinates();
    void setTopDistance(const int distance);
    void resumeTopDistance(const int distance);
    int getTopDistance();
    void leftStepper(const int dir);
    void rightStepper(const int dir);
    int extendToHome();
    void runSteppers();
    float beginLinearTravel(double x, double y, int speed);

    // Used for calibration of the esteps.
    void extend1000mm(); 

    Point getHomeCoordinates();
    void disableMotors();
};

#endif

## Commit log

2022-07-26 added servo
2022-10-23 changing to new actuator
2022-10-23 finished new servo code
2023-03-21 added pen servo
2023-03-28 slow servo
2023-03-28 interpolating movement, not working
    [movement.cpp, movement.h, runner.cpp]
2023-04-05 added oled display and somehow fixed the problem
    [main.cpp, movement.cpp, movement.h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]
2023-04-08 restored pen calibration
2023-04-13 fixed sleep step, added esteps calibration
    [main.cpp, movement.cpp, movement.h]
2023-04-16 switched to accelstepper lib
2023-08-04 disabled motor rest for now
2023-08-05 slower print and more sleep
2023-08-19 switched to accelsteppers
2023-09-17 added bom
2023-09-17 updated bom
2023-09-17 more bom updates
2023-09-17 added stls
    [Bottom.stl, PD clamp.stl, cover.stl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]
2023-09-20 added bolt lengths
2023-09-21 belt loops
    [belt loop - left.stl, belt loop - right.stl]
2023-09-21 added servo clamp
    [servo clamp.stl]
2023-10-10 fixed race condition in runner
    [runner.cpp]
2023-10-16 added 1mm buffer
2023-12-18 fixed extend to home to not require a client
    [main.cpp, movement.cpp, movement.h]
2024-02-15 new stls, untested
    [Bottom.stl, PD clamp.stl, belt loop - left.stl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]
2024-04-08 updated stls
    [PD clamp.stl, black parts.3mf, bottom.stl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]
2024-04-09 homing text
2024-04-26 deleted old wiring
2024-05-19 added reset when connected via captive portal
    [main.cpp]
2024-06-09 updated parts for the latest revision
    [PD clamp.stl, black parts.3mf, bottom.stl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]
2024-07-29 steppers initialized first to avoid creep
    [main.cpp]
2024-10-03 fixed white parts layout
    [white parts.3mf]
2024-11-15 fixed slicer and order of frames, transform still broken
    [commandhandlingphase.cpp, main.cpp, phasemanager.cpp]
2024-12-04 bottom pd hole depth fixed
    [bottom.stl, white parts.3mf]
2024-12-06 updated BOM with prices
2025-02-12 changed power supply to 30w
2025-03-16 removed bolts
2025-03-21 bom list
2025-03-21 bom page complete
2025-03-21 update BOM links
2025-03-21 removed links from bom
2025-03-26 new version of esp server and park servo fix
    [phasemanager.cpp]
2025-03-27 fixed file upload and esteps calibration, and pinned all versions
    [main.cpp, phasemanager.cpp]
2025-04-18 restored path tracer. needs testing
2025-05-21 Adding holes to the bottom STL for accessing ESP32 buttons while in assembly.
    [bottom.stl]
2025-05-21 wip incl. calibration fix
    [movement.cpp, movement.h]
2025-05-21 estep calibration: fixing sign error for right motor. Chaning lenght to 1000mm for better accuracy.
    [movement.cpp, movement.h]
2025-05-21 fix: belt offset error
    [movement.h]
2025-05-22 WIP: Introducting new constants for belt length computation.
2025-05-22 Adding torque computation.
2025-05-22 Torque computation complete.
2025-05-23 fixing belt offset calibration bug; some cleanup of movement.h
    [movement.cpp, movement.h]
2025-05-26 max spiffs partition size
    [partitions.csv]
2025-05-26 kinematic model v1.0
2025-05-26 added translation of pen center to TangentPoints. Works! (1.5mm error)
    [movement.cpp]
2025-05-27 removing debug prints
2025-05-27 reverting some changes for PR
    [bottom.stl]
2025-05-27 applying typo fixes from PR branch
    [movement.cpp, movement.h]
2025-05-27 fixing torque out of bounds error
    [movement.cpp]
2025-05-27 fixing bug: solveTorqueEquilibrium search window too small
    [movement.cpp]
2025-05-27 Starting doc kinematic model
2025-05-28 kinematic model, first draft complete
2025-05-28 KinematicModel.md V1.0
2025-08-28 new servo lib ver for new platform
2025-09-10 update bom
2025-09-13 updated 3mf
    [black parts.3mf, white parts.3mf]
2026-04-13 no more claude mount
2026-04-14 claude mount, dpad fix, svg fix
2026-05-04 more margin, less jog speed, reset to defaults
    [movement.h]
2026-05-04 boundary clamping for zigzag
2026-05-20 corrected d_t to use 85.90 spacing
    [movement.h]
2026-05-28 pen width up to 2mm
2026-05-31 lower limit for the new rack and pinion pen driver
